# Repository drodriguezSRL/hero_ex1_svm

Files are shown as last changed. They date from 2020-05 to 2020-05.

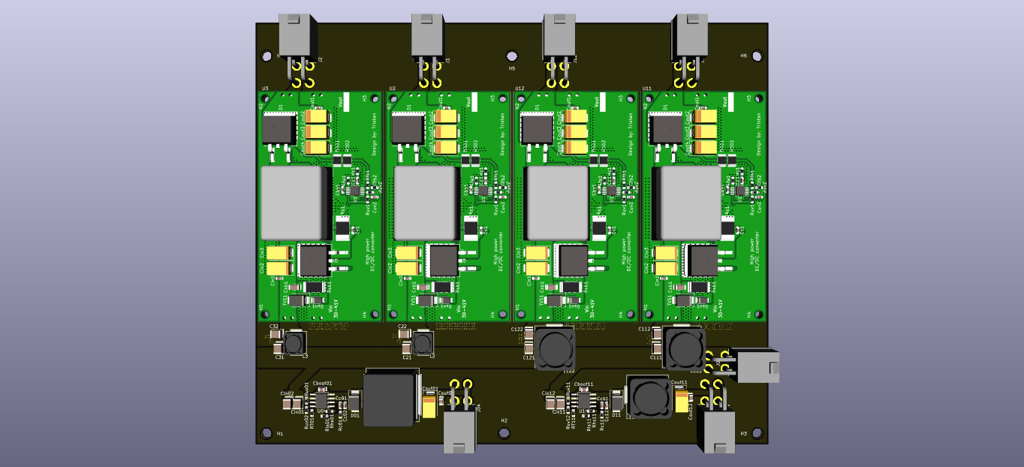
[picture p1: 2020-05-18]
Service Module/Power Conditioning & Distribution Electronics/Power Supply Unit/High_power__DC_DC_board/Doc/Power_board_preview_top.png

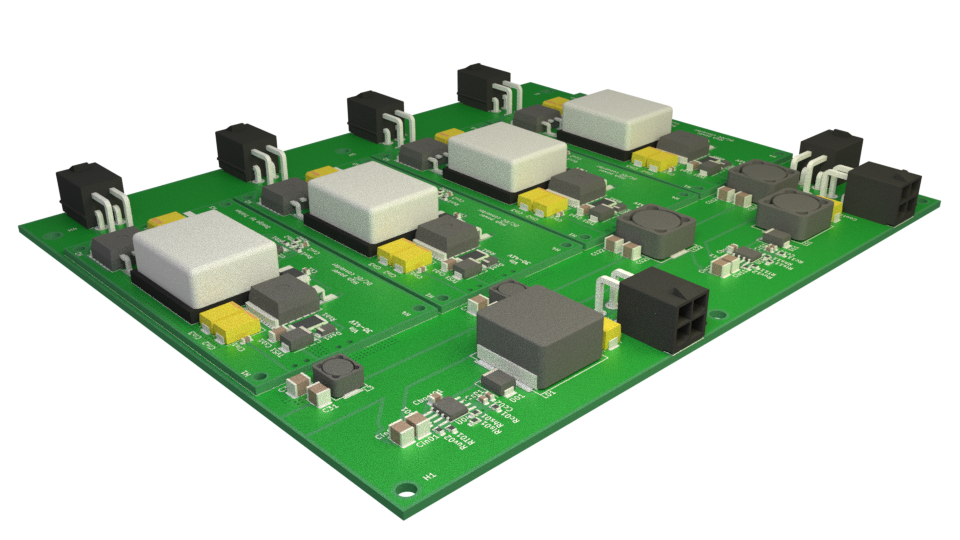
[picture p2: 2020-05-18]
Service Module/Power Conditioning & Distribution Electronics/Power Supply Unit/High_power__DC_DC_board/Doc/low_res_power_board.png

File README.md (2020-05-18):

# HERO Explorer 1 Rover - Service Module (SVM)

The following contains all the design files (i.e., kiCad project files) for the PCBs inside the service module. That includes the Power Supply Unit (PSU), Power Distribution Unit (PDU), and the Rocker Interface Unit (RIU).  3D graphics files are also included (.step and .stl).

## Versioning

High-speed Exploration Rover Team, Explorer 1 Service Module SVM Version 1. Rev. 0.

## Authors

* **David Rodriguez** - *Head of the project*
* **Alan Allart** - *Electronics & Low-level developer*

See also a list of contributors

* **Kazuki Nakagoshi** - *Manufacturing & International relationships*
* **Tristan Lecocq** - *Power system*
* **Sayo Sugimori** - *Secretary*
* **Kazuya Yoshida** - *Professor, Space Robotics Lab*

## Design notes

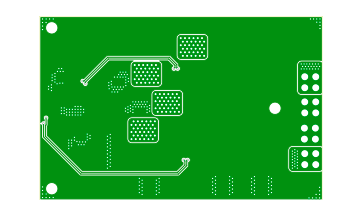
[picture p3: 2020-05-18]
Service Module/Power Conditioning & Distribution Electronics/Power Supply Unit/High_power_DC_DC_buck_boost_converter/Buck_boost/Doc/Buck_boost-brd.png

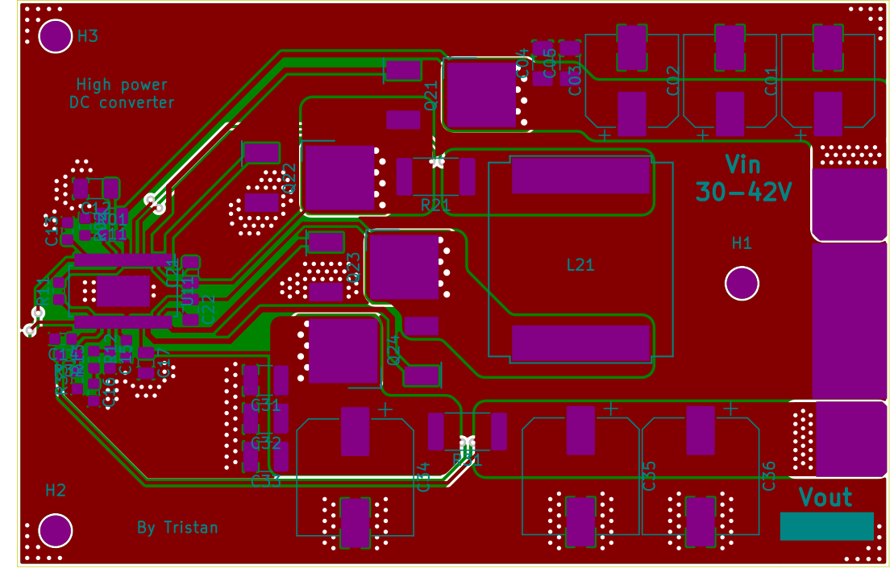
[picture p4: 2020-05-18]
Service Module/Power Conditioning & Distribution Electronics/Power Supply Unit/High_power_DC_DC_buck_boost_converter/Buck_boost/Doc/PCB.png

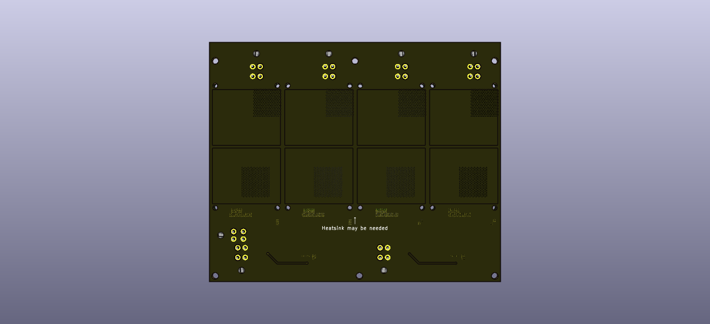
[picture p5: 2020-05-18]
Service Module/Power Conditioning & Distribution Electronics/Power Supply Unit/High_power__DC_DC_board/Doc/Power_board_preview_bot.png

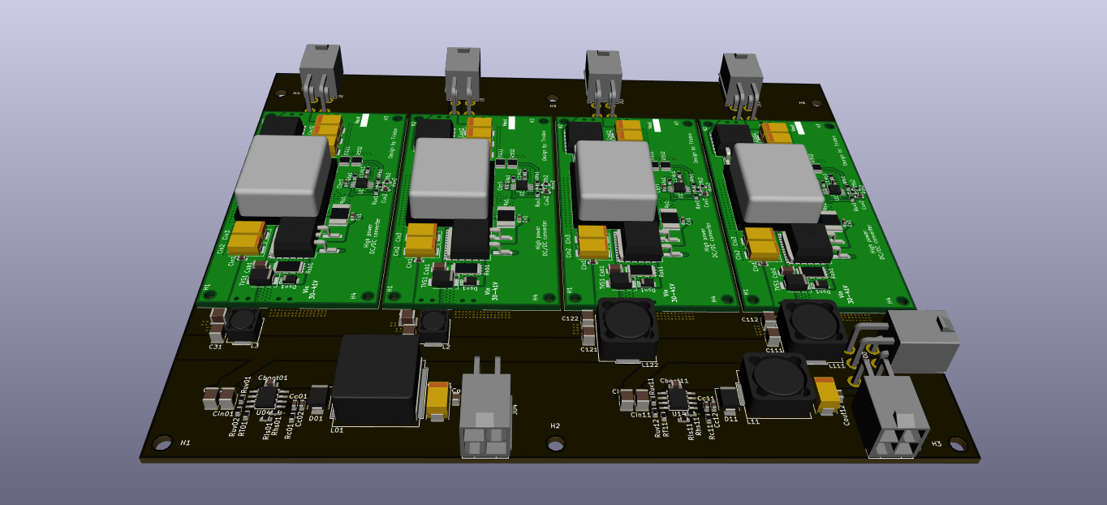
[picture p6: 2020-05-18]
Service Module/Power Conditioning & Distribution Electronics/Power Supply Unit/High_power__DC_DC_board/Doc/Power_board_preview.png

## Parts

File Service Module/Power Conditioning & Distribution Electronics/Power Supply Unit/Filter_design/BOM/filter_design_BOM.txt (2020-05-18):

###########################################
#   Bill of materials for Filter Design   #
###########################################

Prices are took from Mouser.jp website

#############################################

    Description         Reference           nb      price(¥)    unit_price(¥)

    10u L IDC>7.5A      744373965100        2       654,8       327.4
    10u L IDC>3.5A      PA4341.103ANLT      2       244.6       122.3
    1210 470n / 50V C   C1210C474K5RACTU    8       252         31.5 

#############################################

Total components price (per board): 1151,4¥

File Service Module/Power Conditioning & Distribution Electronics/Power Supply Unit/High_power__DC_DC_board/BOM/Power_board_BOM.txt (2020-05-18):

#############################################
#   Bill of materials for Power Board PCB   #
#############################################

Prices are took from Mouser.jp website

#############################################

Name            Description     Reference           nb      price(¥)    unit_price(¥)

Buck converter:
U05,U15         ADJ converter   TPS54560BDDA        x2      1367,8      683.9

Passive components:
Cboot           0.1u/50V C      885012206095        x2      23.4        11.7
Cc01            27n/25V C       CC0603KRX7R8BB273   x1      14          14
Cc02            680p/25V C      885012206058        x1      11.7        11.7
Cc11            18n/25V C       CC0603KRX7R8BB183   x1      14          14
Cc12            1n/25V C        CC0603KRX7R8BB102   x1      11.7        11.7
Cin             10u/50V C       GRM32ER71H106MA12L  x4      447,2       111.8
Cout01,Cout11   47u/50V CP      T495X476K035ATE230  x2      549,8       274.9
Cout02,Cout12   100n/50V C      885012207098        x2      23.4        11.7
D01,D02         Shottky D       NRVTSS5100ET3G      x2      109,6       54.8
L01             47u/3A L        177CDMCCDS-470MC    x1      454.4       454.4
L11             22u/3A L        125CDMCCDS-220MC    x1      210.9       210.9
Rc01            0603 6.8k R     CRCW06036K80FKEA    x1      11.7        11.7
Rc11            0603 4.42k R    CRCW06034K42FKEA    x1      11.7        11.7
Rhs01           0603 46.4k R    CRCW060346K4FKEA    x1      11.7        11.7
Rhs11           0603 17.4k R    CRCW060317K4FKEA    x1      11.7        11.7
Rls01,Rls11     0603 3.3k R     CRCW06033K30FKEA    x2      23.4        11.7
RT01,RT11       0603 243k R     CRCW0603243KFKEA    x2      23.4        11.7
Ruv01,Ruv11     0603 294k R     CRCW0603294KFKEA    x2      23.4        11.7
Ruv02,Ruv12     0603 12.1k R    CRCW060312K1FKEA    x2      23.4        11.7

Connectors :
JXX             Molex conn      172448-0004         x7      611,8       87.4

#############################################

Total components price (per board): 3990,1¥

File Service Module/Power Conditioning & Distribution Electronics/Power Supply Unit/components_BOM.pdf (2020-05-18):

## Components listing for 4 High power DC/DC converter modules + 1 Power Board

### Price taken from Mouser.jp website without quantity price reduction

Component ref. | Description | Purchase link | Number

DC/DC module components
LT8390EFE#PBF | Buck + boost DC controller | 1277,8 | 5 | 6389
NTD5C668NLT4G | Power N-MOSFET | 188,4 | 20 | 3768
EEETG1H470P | 47uF / 50V electrolytic filtering capacitor | 108,9 | 15 | 1633,5
EEETG1H100P | 10uF / 50V electrolytic filtering capacitor | 88,5 | 15 | 1327,5
GCM32EL8EH106KA07L | 10uF / 50V ceramic filtering capacitor | 144,1 | 15 | 2161,5
C1206C475M5RACAUTO | 4,7uF / 50V ceramic filtering capacitor | 77,2 | 10 | 772
C0805X104K1RAC3316 | 0,1uF / 100V bootstrap capacitor | 49,9 | 10 | 499
CC0805KFX7R9BB105 | 1uF / 50V decoupling capacitor | 29,5 | 10 | 295
CC1206KKX5R9BB475 | 4,7uF / 50V decoupling capacitor | 81,7 | 6 | 490,2
CC0603KRX5R9BB474 | 0,47uF / 50V decoupling capacitor | 67 | 6 | 402
CC0603JPX7R9BB104 | 0,1uF / 50V soft start capacitor | 14,8 | 6 | 88,8
CC0603GPNPO9BN101 | 100pF / 50V compensation capacitor | 14,8 | 6 | 88,8
CC0603KRX7R9BB472 | 4,7nF / 50V compensation capacitor | 11,3 | 6 | 67,8
CRCW0603120KFKEA | 120k UVLO resistor | 11,3 | 6 | 67,8
CRCW06035K10FKEA | 5,1k UVLO resistor | 11,3 | 6 | 67,8
CRCW0603100KFKEA | | 11,3 | 20 | 226
CRCW060327K0JNEA | 27k compensation resistor | 11,3 | 6 | 67,8
PA4344.333ANLT | 33uH / 12A High power inductor | 514,1 | 6 | 3084,6
CRCW0603150KFKEA | 150k FB resistor (36V reg) | 11,3 | 4 | 45,2
TNPW06034K27BEEA | 4,27k FB resistor (36V reg) | 76 | 4 | 304
PMR100HZPJU9L0 | 9mOhm / 2W shunt resistor | 56,7 | 3 | 170,1
RLP73V3AR011FTDF | 11mOhm / 2W shunt resistor | 85,1 | 6 | 510,6
RT0603DRE077K41L | 7,41k FB resistor (14,5V reg) | 14,8 | 2 | 29,6
RLP73V3AR013FTDF | 13mOhm / 2W shunt resistor | 85,1 | 3 | 255,3
CRCW06034K30FKEA | 4,3k FB resistor (24V reg) | 11,3 | 2 | 22,6
| | | | 22834,5
Filtering components
744373965100 | IDC=8,8A 10uH filtering inductor | 327,4 | 3 | 982,2
PA4341.103ANLT | IDC=4A 10uH filtering inductor | 122,3 | 3 | 366,9
C1210C474K5RACTU | 470nF / 50V filtering capacitor | 31,5 | 10 | 315
| | PRICE | 16 | 1664,1
Power Board components
TPS54560BDDA | 5A adustable buck converter | 683,9 | 4 | 2735,6
885012206095 | 0,1uF / 50V bootstap capacitor | 11,7 | 4 | 46,8
CC0603KRX7R8BB273 | 27nF / 25V Compensation capacitor | 14 | 2 | 28
885012206058 | 680pF / 25V Compensation capacitor | 11,7 | 2 | 23,4
CC0603KRX7R8BB183 | 18nF / 25V Compensation capacitor | 14 | 2 | 28
CC0603KRX7R8BB102 | 1nF / 25V Compensation capacitor | 11,7 | 2 | 23,4
GRM32ER71H106MA12L | 10uF / 50V Input capacitor | 111,8 | 8 | 894,4
T495X476K035ATE230 | 47uF / 50V Output tantalum capacitor | 274,9 | 4 | 1099,6
885012207098 | 100nF / 50V Output ceramic capacitor | 11,7 | 4 | 46,8
NRVTSS5100ET3G | Schottky rectifier diode | 54,8 | 4 | 219,2
177CDMCCDS-470MC | 47uH fixed inductor | 454,4 | 2 | 908,8
125CDMCCDS-220MC | 22uH fixed inductor | 210,9 | 2 | 421,8
CRCW06036K80FKEA | 0603 6,8kOhm compensation resistor | 11,7 | 2 | 23,4
CRCW06034K42FKEA | 0603 4,42kOhm compensation resistor | 11,7 | 2 | 23,4
CRCW060346K4FKEA | 0603 46,4kOhm feedback resistor | 11,7 | 2 | 23,4
CRCW060317K4FKEA | 0603 17,4kOhm feedback resistor | 11,7 | 2 | 23,4
CRCW06033K30FKEA | 0603 3,3kOhm feedback resistor | 11,7 | 4 | 46,8
CRCW0603243KFKEA | 0603 243kOhm frequency set resistor | 11,7 | 4 | 46,8
CRCW0603294KFKEA | 0603 294kOhm undervoltage resistor | 11,7 | 4 | 46,8
CRCW060312K1FKEA | 0603 12,1k undervoltage resistor | 11,7 | 4 | 46,8
172448-0004 | 13A/contact horizontal Molex connectors | 87,4 | 10 | 874
| | PRICE | 74 | 7630,6
Other
TS391AX10 | Solder paste | 3139,7 | 1 | 3139,7
100500F00000G | Thermal paste | 3458,9 | 1 | 3458,9
| | PRICE | 2 | 6598,6
TOTAL PRICE | 92 | 38727,8
Unit price ( ¥ ) | Price ( ¥ )

https://www.mouser.jp/ProductDetail/Analog-Devices-Linear-Technology/LT8390EFEPBF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
100k FB / frequency set / bias resistor | https://www.mouser.jp/ProductDetail/Vishay-Dale/CRCW0603100KFKEA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
https://www.mouser.jp/ProductDetail/Vishay-Dale/CRCW060327K0JNEA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

https://www.mouser.jp/ProductDetail/Wurth-Elektronik/744373965100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

https://www.mouser.jp/ProductDetail/Texas-Instruments/TPS54560BDDA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

https://www.mouser.jp/ProductDetail/Chip-Quik/TS391AX10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

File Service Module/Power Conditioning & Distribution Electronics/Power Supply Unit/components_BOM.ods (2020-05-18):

Components listing for 4 High power DC/DC converter modules + 1 Power Board
Price taken from Mouser.jp website without quantity price reduction
Component ref. | Description | Purchase link | Unit price ( ¥ ) | Number | Price ( ¥ )
DC/DC module components
LT8390EFE#PBF | Buck + boost DC controller | https://www.mouser.jp/ProductDetail/Analog-Devices-Linear-Technology/LT8390EFEPBF | 1277,8 | 5 | 6389
NTD5C668NLT4G | Power N-MOSFET | https://www.mouser.jp/ProductDetail/ON-Semiconductor/NTD5C668NLT4G | 188,4 | 20 | 3768
EEETG1H470P | 47uF / 50V electrolytic filtering capacitor | https://www.mouser.jp/ProductDetail/Panasonic/EEE-TG1H470P | 108,9 | 15 | 1633,5
EEETG1H100P | 10uF / 50V electrolytic filtering capacitor | https://www.mouser.jp/ProductDetail/Panasonic/EEE-TG1H100P | 88,5 | 15 | 1327,5
GCM32EL8EH106KA07L | 10uF / 50V ceramic filtering capacitor | https://www.mouser.jp/ProductDetail/Murata-Electronics/GCM32EL8EH106KA07L | 144,1 | 15 | 2161,5
C1206C475M5RACAUTO | 4,7uF / 50V ceramic filtering capacitor | https://www.mouser.jp/ProductDetail/KEMET/C1206C475M5RACAUTO | 77,2 | 10 | 772
C0805X104K1RAC3316 | 0,1uF / 100V bootstrap capacitor | https://www.mouser.jp/ProductDetail/KEMET/C0805X104K1RAC3316 | 49,9 | 10 | 499
CC0805KFX7R9BB105 | 1uF / 50V decoupling capacitor | https://www.mouser.jp/ProductDetail/Yageo/CC0805KFX7R9BB105 | 29,5 | 10 | 295
CC1206KKX5R9BB475 | 4,7uF / 50V decoupling capacitor | https://www.mouser.jp/ProductDetail/Yageo/CC1206KKX5R9BB475 | 81,7 | 6 | 490,2
CC0603KRX5R9BB474 | 0,47uF / 50V decoupling capacitor | https://www.mouser.jp/ProductDetail/Yageo/CC0603KRX5R9BB474 | 67 | 6 | 402
CC0603JPX7R9BB104 | 0,1uF / 50V soft start capacitor | https://www.mouser.jp/ProductDetail/Yageo/CC0603JPX7R9BB104 | 14,8 | 6 | 88,8
CC0603GPNPO9BN101 | 100pF / 50V compensation capacitor | https://www.mouser.jp/ProductDetail/Yageo/CC0603GPNPO9BN101 | 14,8 | 6 | 88,8
CC0603KRX7R9BB472 | 4,7nF / 50V compensation capacitor | https://www.mouser.jp/ProductDetail/Yageo/CC0603KRX7R9BB472 | 11,3 | 6 | 67,8
CRCW0603120KFKEA | 120k UVLO resistor | https://www.mouser.jp/ProductDetail/Vishay-Dale/CRCW0603120KFKEA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 | 11,3 | 6 | 67,8
CRCW06035K10FKEA | 5,1k UVLO resistor | https://www.mouser.jp/ProductDetail/Vishay-Dale/CRCW06035K10FKEA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 | 11,3 | 6 | 67,8
CRCW0603100KFKEA | 100k FB / frequency set / bias resistor | https://www.mouser.jp/ProductDetail/Vishay-Dale/CRCW0603100KFKEA | 11,3 | 20 | 226
CRCW060327K0JNEA | 27k compensation resistor | https://www.mouser.jp/ProductDetail/Vishay-Dale/CRCW060327K0JNEA | 11,3 | 6 | 67,8
PA4344.333ANLT | 33uH / 12A High power inductor | https://www.mouser.jp/ProductDetail/Pulse-Electronics/PA4344333ANLT | 514,1 | 6 | 3084,6
CRCW0603150KFKEA | 150k FB resistor (36V reg) | https://www.mouser.jp/ProductDetail/Vishay-Dale/CRCW0603150KFKEA | 11,3 | 4 | 45,2
TNPW06034K27BEEA | 4,27k FB resistor (36V reg) | https://www.mouser.jp/ProductDetail/Vishay/TNPW06034K27BEEA | 76 | 4 | 304
PMR100HZPJU9L0 | 9mOhm / 2W shunt resistor | https://www.mouser.jp/ProductDetail/ROHM-Semiconductor/PMR100HZPJU9L0 | 56,7 | 3 | 170,1
RLP73V3AR011FTDF | 11mOhm / 2W shunt resistor | https://www.mouser.jp/ProductDetail/TE-Connectivity-Holsworthy/RLP73V3AR011FTDF | 85,1 | 6 | 510,6
RT0603DRE077K41L | 7,41k FB resistor (14,5V reg) | https://www.mouser.jp/ProductDetail/Yageo/RT0603DRE077K41L | 14,8 | 2 | 29,6
RLP73V3AR013FTDF | 13mOhm / 2W shunt resistor | https://www.mouser.jp/ProductDetail/TE-Connectivity-Holsworthy/RLP73V3AR013FTDF | 85,1 | 3 | 255,3
CRCW06034K30FKEA | 4,3k FB resistor (24V reg) | https://www.mouser.jp/ProductDetail/Vishay-Dale/CRCW06034K30FKEA | 11,3 | 2 | 22,6
 |  |  |  |  | 22834,5
Filtering components
744373965100 | IDC=8,8A 10uH filtering inductor | https://www.mouser.jp/ProductDetail/Wurth-Elektronik/744373965100 | 327,4 | 3 | 982,2
PA4341.103ANLT | IDC=4A 10uH filtering inductor | https://www.mouser.jp/ProductDetail/Pulse-Electronics/PA4341103ANLT | 122,3 | 3 | 366,9
C1210C474K5RACTU | 470nF / 50V filtering capacitor | https://www.mouser.jp/ProductDetail/KEMET/C1210C474K5RACTU?qs=sGAEpiMZZMs0AnBnWHyRQM0yVqKBBK3frSa2n3pwvnQ%3D | 31,5 | 10 | 315
 |  |  | PRICE | 16 | 1664,1
Power Board components
TPS54560BDDA | 5A adustable buck converter | https://www.mouser.jp/ProductDetail/Texas-Instruments/TPS54560BDDA | 683,9 | 4 | 2735,6
885012206095 | 0,1uF / 50V bootstap capacitor | https://www.mouser.jp/ProductDetail/Wurth-Elektronik/885012206095 | 11,7 | 4 | 46,8
CC0603KRX7R8BB273 | 27nF / 25V Compensation capacitor | https://www.mouser.jp/ProductDetail/Yageo/CC0603KRX7R8BB273 | 14 | 2 | 28
885012206058 | 680pF / 25V Compensation capacitor | https://www.mouser.jp/ProductDetail/Wurth-Elektronik/885012206058 | 11,7 | 2 | 23,4
CC0603KRX7R8BB183 | 18nF / 25V Compensation capacitor | https://www.mouser.jp/ProductDetail/Yageo/CC0603KRX7R8BB183 | 14 | 2 | 28
CC0603KRX7R8BB102 | 1nF / 25V Compensation capacitor | https://www.mouser.jp/ProductDetail/Yageo/CC0603KRX7R8BB102 | 11,7 | 2 | 23,4
GRM32ER71H106MA12L | 10uF / 50V Input capacitor | https://www.mouser.jp/ProductDetail/Murata-Electronics/GRM32ER71H106MA12L | 111,8 | 8 | 894,4
T495X476K035ATE230 | 47uF / 50V Output tantalum capacitor | https://www.mouser.jp/ProductDetail/KEMET/T495X476K035ATE230 | 274,9 | 4 | 1099,6
885012207098 | 100nF / 50V Output ceramic capacitor | https://www.mouser.jp/ProductDetail/Wurth-Elektronik/885012207098 | 11,7 | 4 | 46,8
NRVTSS5100ET3G | Schottky rectifier diode | https://www.mouser.jp/ProductDetail/ON-Semiconductor/NRVTSS5100ET3G | 54,8 | 4 | 219,2
177CDMCCDS-470MC | 47uH fixed inductor | https://www.mouser.jp/ProductDetail/Sumida/177CDMCCDS-470MC | 454,4 | 2 | 908,8
125CDMCCDS-220MC | 22uH fixed inductor | https://www.mouser.jp/ProductDetail/Sumida/125CDMCCDS-220MC | 210,9 | 2 | 421,8
CRCW06036K80FKEA | 0603 6,8kOhm compensation resistor | https://www.mouser.jp/ProductDetail/Vishay-Dale/CRCW06036K80FKEA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 | 11,7 | 2 | 23,4
CRCW06034K42FKEA | 0603 4,42kOhm compensation resistor | https://www.mouser.jp/ProductDetail/Vishay-Dale/CRCW06034K42FKEA | 11,7 | 2 | 23,4
CRCW060346K4FKEA | 0603 46,4kOhm feedback resistor | https://www.mouser.jp/ProductDetail/Vishay-Dale/CRCW060346K4FKEA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 | 11,7 | 2 | 23,4
CRCW060317K4FKEA | 0603 17,4kOhm feedback resistor | https://www.mouser.jp/ProductDetail/Vishay-Dale/CRCW060317K4FKEA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 | 11,7 | 2 | 23,4
CRCW06033K30FKEA | 0603 3,3kOhm feedback resistor | https://www.mouser.jp/ProductDetail/Vishay-Dale/CRCW06033K30FKEA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 | 11,7 | 4 | 46,8
CRCW0603243KFKEA | 0603 243kOhm frequency set resistor | https://www.mouser.jp/ProductDetail/Vishay-Dale/CRCW0603243KFKEA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 | 11,7 | 4 | 46,8
CRCW0603294KFKEA | 0603 294kOhm undervoltage resistor | https://www.mouser.jp/ProductDetail/Vishay-Dale/CRCW0603294KFKEA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 | 11,7 | 4 | 46,8
CRCW060312K1FKEA | 0603 12,1k undervoltage resistor | https://www.mouser.jp/ProductDetail/Vishay-Dale/CRCW060312K1FKEA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 | 11,7 | 4 | 46,8
172448-0004 | 13A/contact horizontal Molex connectors | https://www.mouser.jp/ProductDetail/Molex/172448-0004 | 87,4 | 10 | 874
 |  |  | PRICE | 74 | 7630,6
Other
TS391AX10 | Solder paste | https://www.mouser.jp/ProductDetail/Chip-Quik/TS391AX10 | 3139,7 | 1 | 3139,7
100500F00000G | Thermal paste | https://www.mouser.jp/ProductDetail/Aavid/100500F00000G | 3458,9 | 1 | 3458,9
 |  |  | PRICE | 2 | 6598,6
 |  |  | TOTAL PRICE | 92 | 38727,8

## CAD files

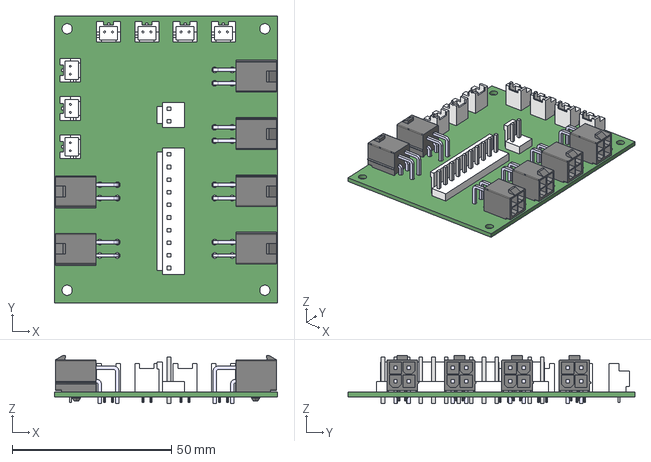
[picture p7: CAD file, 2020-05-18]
Service Module/Power Conditioning & Distribution Electronics/Power Distribution Unit/PowerDistributionUnit.step
70.0 x 90.0 x 15.1 mm

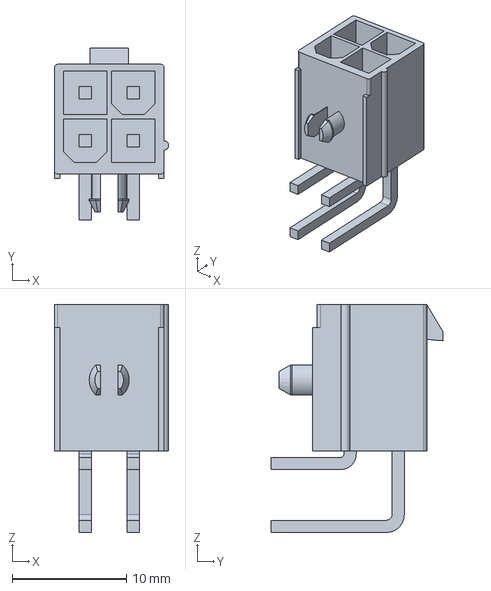
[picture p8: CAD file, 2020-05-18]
Service Module/Power Conditioning & Distribution Electronics/Power Supply Unit/High_power__DC_DC_board/power_board/3d_model/Molex_horizontal_1724480004.stp
10.0 x 15.0 x 19.9 mm

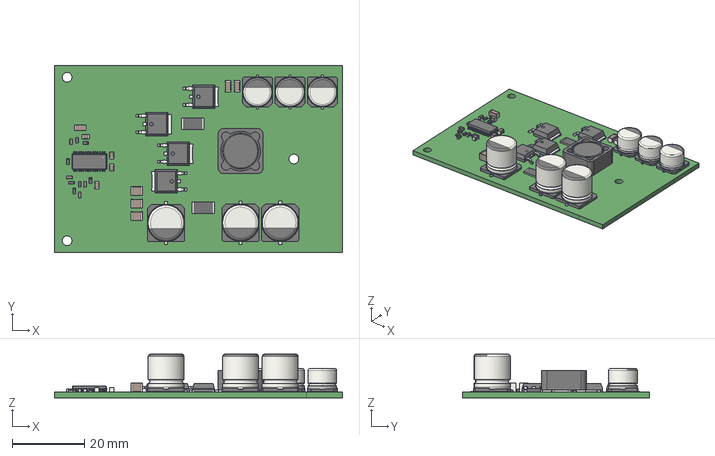
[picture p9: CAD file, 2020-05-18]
Service Module/Power Conditioning & Distribution Electronics/Power Supply Unit/High_power_DC_DC_buck_boost_converter/Buck_boost/3d_model/Buck_boost.step
80.0 x 52.0 x 12.2 mm

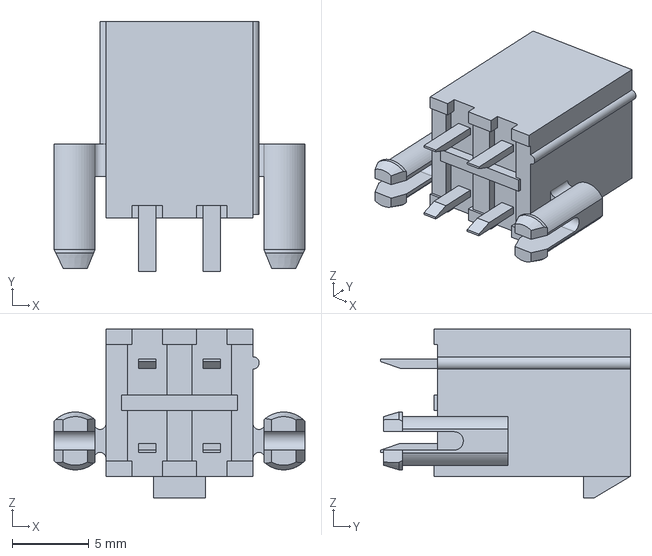
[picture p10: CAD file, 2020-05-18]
Service Module/Power Conditioning & Distribution Electronics/Power Supply Unit/High_power__DC_DC_board/power_board/3d_model/Molex_vertical_1726750413.stp
16.4 x 16.3 x 11.0 mm

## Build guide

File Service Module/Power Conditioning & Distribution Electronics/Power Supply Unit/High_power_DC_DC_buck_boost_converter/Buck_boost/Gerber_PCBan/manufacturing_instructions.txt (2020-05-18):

Buck-boost-F_Cu.gtl（部品面パターン）

Buck-boost-B_Cu.gbl（半田面パターン）

Buck-boost-F_Mask.gts（部品面パターン）

Buck-boost-B_Mask.gbs（半田面パターン）

Buck-boost-F_SilkS.gto（部品面パターン）

Buck-boost-B_SilkS.gbo（半田面パターン）

Buck-boost-Edge_Cuts.gm1　（基板外形）

Buck-boost.drl （ドリルデータ）

Buck-boost-drl_map.gbr（ドリルマップ）

Buck-boost-drl.rpt (ドリルリスト）

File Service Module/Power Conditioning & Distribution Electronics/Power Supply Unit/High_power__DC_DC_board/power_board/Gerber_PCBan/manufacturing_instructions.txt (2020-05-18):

High_power__DC_DC_board-F_Cu.gtl（部品面パターン）

High_power__DC_DC_board-B_Cu.gbl（半田面パターン）

High_power__DC_DC_board-F_Mask.gts（部品面パターン）

High_power__DC_DC_board-B_Mask.gbs（半田面パターン）

High_power__DC_DC_board-F_SilkS.gto（部品面パターン）

High_power__DC_DC_board-B_SilkS.gbo（半田面パターン）

High_power__DC_DC_board-Edge_Cuts.gm1　（基板外形）

High_power__DC_DC_board.drl （ドリルデータ）

High_power__DC_DC_board-drl_map.gbr（ドリルマップ）

High_power__DC_DC_board-drl.rpt (ドリルリスト）

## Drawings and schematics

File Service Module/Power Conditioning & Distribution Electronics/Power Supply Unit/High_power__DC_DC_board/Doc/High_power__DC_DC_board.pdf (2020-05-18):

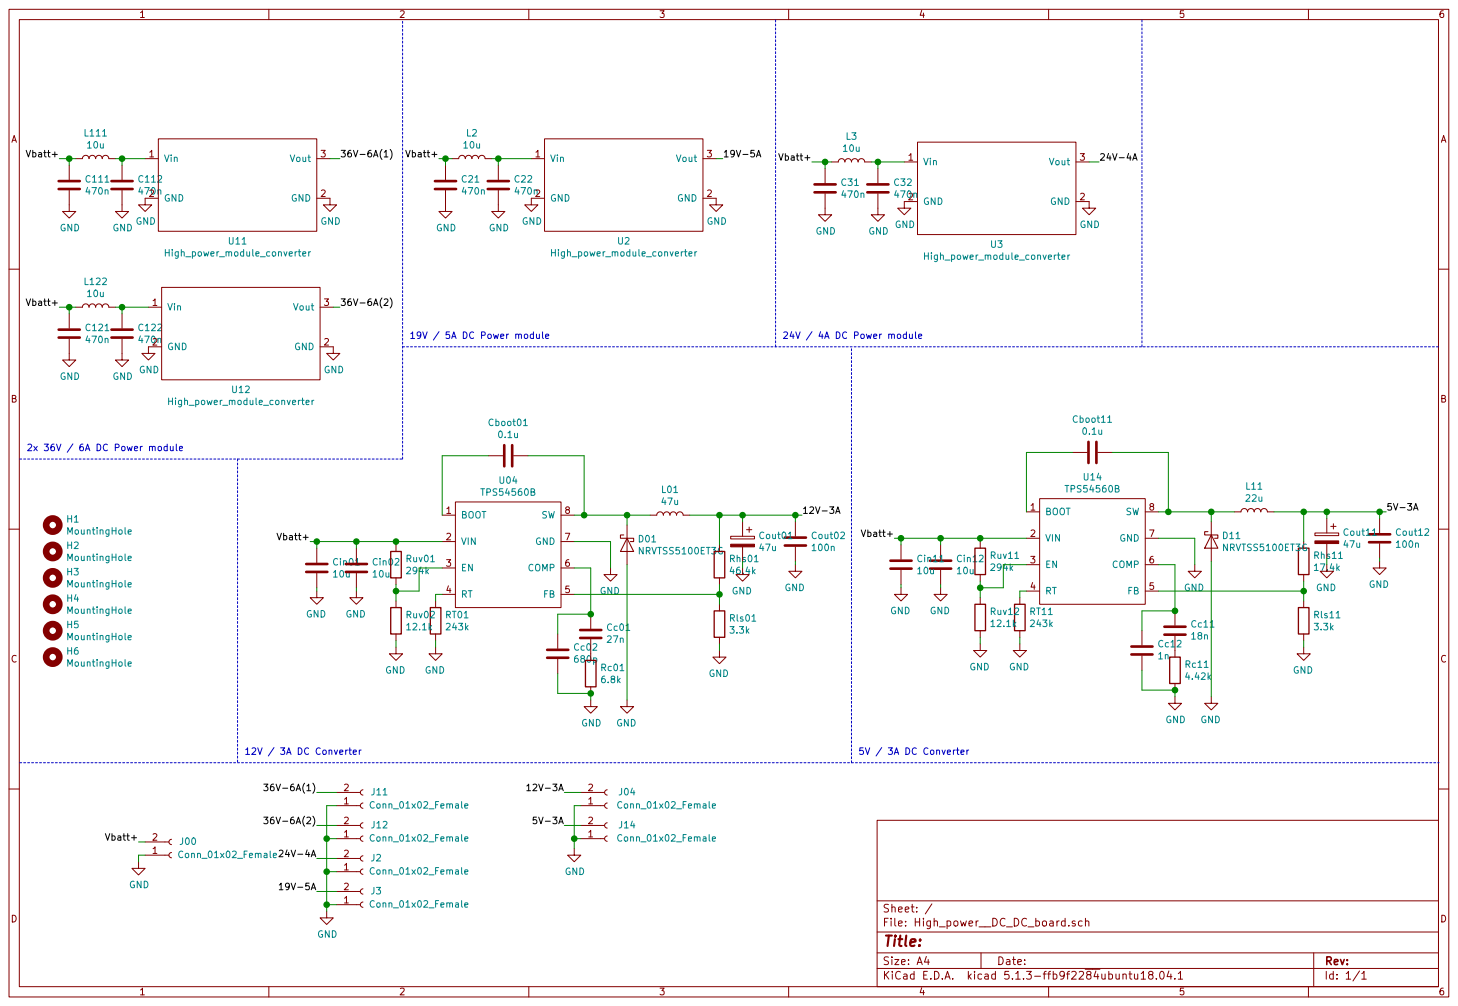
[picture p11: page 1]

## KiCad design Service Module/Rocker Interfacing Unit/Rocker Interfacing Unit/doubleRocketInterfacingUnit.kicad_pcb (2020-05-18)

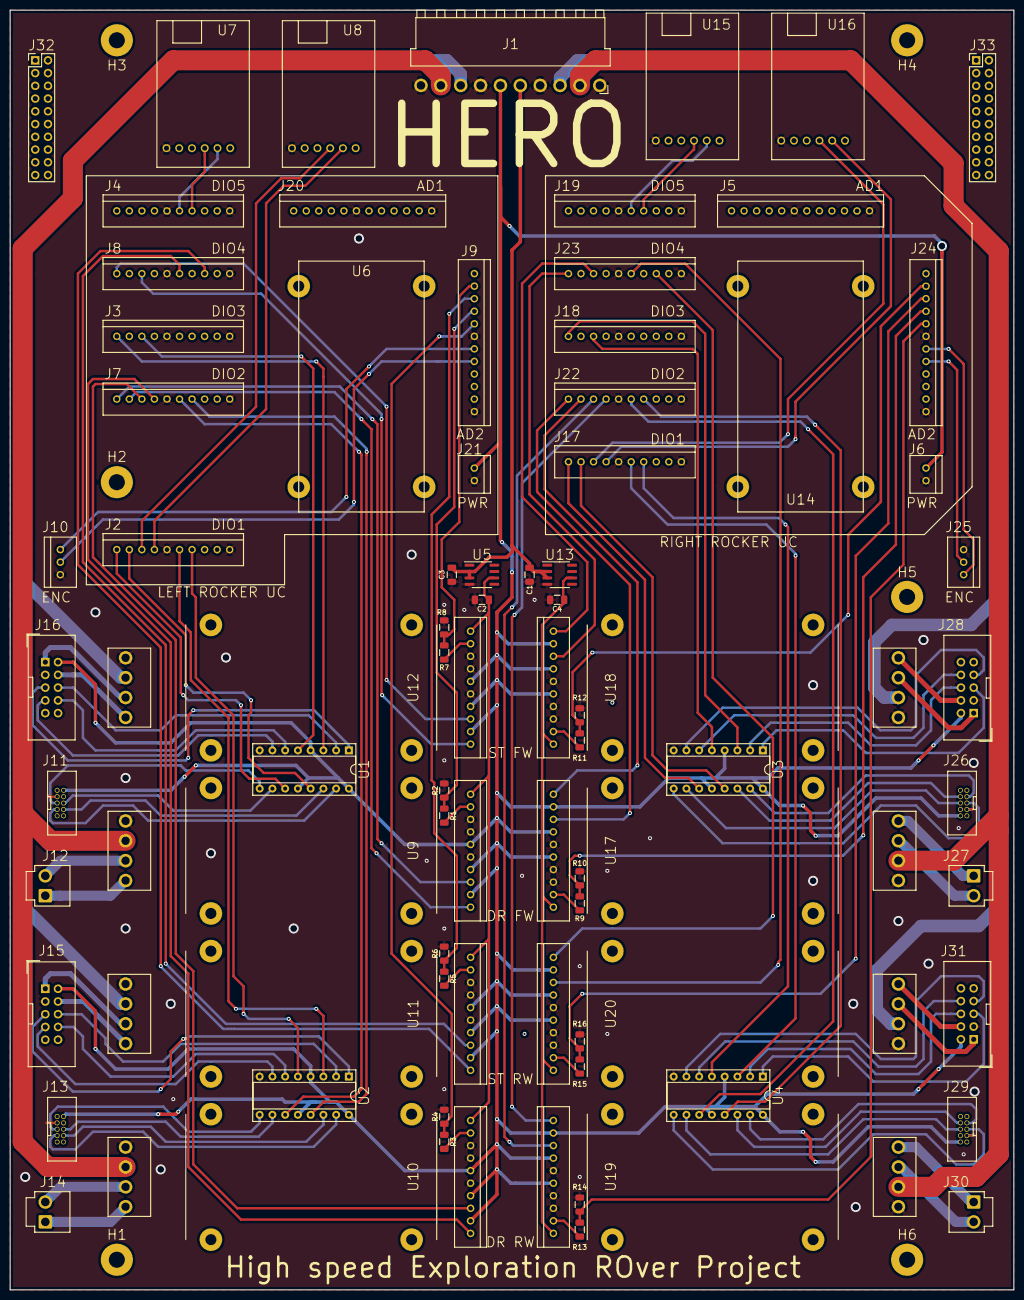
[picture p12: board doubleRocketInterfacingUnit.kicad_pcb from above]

Board: 2 copper layers, 200.0 x 255.0 mm, 79 parts (0 on the bottom side), 115 nets.

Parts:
C1, C3: 1µF; C_1206_3216Metric
C2, C4: 2µF; C_1206_3216Metric
H1, H2, H3, H4, H5, H6: MountingHole; MountingHole_3.2mm_M3_Pad
J1: Conn_01x10; JST_VH_B10PS-VH
J2, J3, J4, J7, J8, J17, J18, J19, J22, J23: Conn_01x10; JST_XA_B10B-XASK-1
J5, J9, J20, J24: Conn_01x12; JST_XA_B12B-XASK-1
J6, J21: Conn_01x02; JST_XA_B2B-XASK-1
J10, J25: Conn_01x03; JST_XA_B3B-XASK-1
J11, J13, J26, J29: Conn_02x05_Odd_Even; SAMTEC_SHF-105-01-L-D-TH
J12, J14, J27, J30: Conn_01x02; JST_VH_B2P-VH
J15, J16, J28, J31: Conn_02x05_Odd_Even; IDC-Header_2x05_P2.54mm_Vertical
J32, J33: Conn_02x10_Odd_Even; PinHeader_2x10_P2.54mm_Vertical
R1, R3, R5, R7, R9, R11, R13, R15: 4k7; R_1206_3216Metric
R2, R4, R6, R8, R10, R12, R14, R16: 9k1; R_1206_3216Metric
U1, U2, U3, U4: SN75175; DIP-16_W7.62mm_SocketAndIC
U5, U13: LT1461CCS8-5; SOIC-8_3.9x4.9mm_P1.27mm
U6, U14: HiBot-Titech-M4; HibotTitechM4
U7, U8, U15, U16: FTDI-Breakout-Board
U9, U10, U11, U12, U17, U18, U19, U20: HiBot-UM-1XH; HibotUM1XH

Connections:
+5V: J1.6, J6.1, J11.2, J13.2, J15.2, J16.2, J21.1, J26.2, J28.2, J29.2, J31.2, U1.4, U1.12, U1.16, U2.4, U2.12, U2.16, U3.4, U3.12, U3.16, U4.4, U4.12, U4.16, U9.5, U9.7, U9.9, U10.5, U10.7, U10.9, U11.5, U11.7, U11.9, U12.5, U12.7, U12.9, U17.5, U17.7, U17.9, U18.5, U18.7, U18.9, U19.5, U19.7, U19.9, U20.5, U20.7, U20.9
+12V: C1.1, C3.1, J1.5, U5.2, U5.3, U13.2, U13.3
+24V: J1.3, J1.8, U11.13, U12.13, U18.13, U20.13
+36V: J1.2, J1.9, U9.13, U10.13, U17.13, U19.13
/Left Rocker Interface/+3V3A: J9.7, J10.1
/Left Rocker Interface/+5VA: C2.1, U5.6, U9.1, U10.1, U11.1, U12.1
/Left Rocker Interface/CUR_DR_FW: J9.4, R1.1, R2.1
/Left Rocker Interface/CUR_DR_RW: J9.5, R3.1, R4.1
/Left Rocker Interface/CUR_ST_FW: J9.2, R7.1, R8.1
/Left Rocker Interface/CUR_ST_RW: J9.3, R5.1, R6.1
/Left Rocker Interface/ENC_DR_FW_1: J2.1, U1.11
/Left Rocker Interface/ENC_DR_FW_2: J2.2, U1.13
/Left Rocker Interface/ENC_DR_RW_1: J7.6, U2.11
/Left Rocker Interface/ENC_DR_RW_2: J7.7, U2.13
/Left Rocker Interface/ENC_ST_FW_1: J3.1, U1.3
/Left Rocker Interface/ENC_ST_FW_2: J3.3, U1.5
/Left Rocker Interface/ENC_ST_RW_1: J2.6, U2.3
/Left Rocker Interface/ENC_ST_RW_2: J2.7, U2.5
/Left Rocker Interface/Left Driving Motor Driver FW/A: J11.6, U1.10
/Left Rocker Interface/Left Driving Motor Driver FW/B: J11.8, U1.14
/Left Rocker Interface/Left Driving Motor Driver FW/~A~: J11.5, U1.9
/Left Rocker Interface/Left Driving Motor Driver FW/~B~: J11.7, U1.15
/Left Rocker Interface/Left Driving Motor Driver RW/A: J13.6, U2.10
/Left Rocker Interface/Left Driving Motor Driver RW/B: J13.8, U2.14
/Left Rocker Interface/Left Driving Motor Driver RW/~A~: J13.5, U2.9
/Left Rocker Interface/Left Driving Motor Driver RW/~B~: J13.7, U2.15
/Left Rocker Interface/Left Steering Motor Driver FW/A: J16.6, U1.2
/Left Rocker Interface/Left Steering Motor Driver FW/B: J16.8, U1.6
/Left Rocker Interface/Left Steering Motor Driver FW/~A~: J16.5, U1.1
/Left Rocker Interface/Left Steering Motor Driver FW/~B~: J16.7, U1.7
/Left Rocker Interface/Left Steering Motor Driver RW/A: J15.6, U2.2
/Left Rocker Interface/Left Steering Motor Driver RW/B: J15.8, U2.6
/Left Rocker Interface/Left Steering Motor Driver RW/~A~: J15.5, U2.1
/Left Rocker Interface/Left Steering Motor Driver RW/~B~: J15.7, U2.7
/Left Rocker Interface/MOT_DR_FW_1: J7.1, U9.8
/Left Rocker Interface/MOT_DR_FW_2: J7.2, U9.10
/Left Rocker Interface/MOT_DR_RW_1: J7.3, U10.8
/Left Rocker Interface/MOT_DR_RW_2: J7.4, U10.10
/Left Rocker Interface/MOT_ST_FW_1: J8.1, U12.8
/Left Rocker Interface/MOT_ST_FW_2: J8.3, U12.10
/Left Rocker Interface/MOT_ST_RW_1: J8.6, U11.8
/Left Rocker Interface/MOT_ST_RW_2: J8.8, U11.10
/Left Rocker Interface/POS_RK: J9.8, J10.2
/Left Rocker Interface/UART_RX_COM: J4.7, U7.3
/Left Rocker Interface/UART_RX_DBG: J2.3, U8.3
/Left Rocker Interface/UART_TX_COM: J4.6, U7.2
/Left Rocker Interface/UART_TX_DBG: J2.4, U8.2
/Right Rocker Interface/+3V3A: J24.7, J25.1
/Right Rocker Interface/+5VA: C4.1, U13.6, U17.1, U18.1, U19.1, U20.1
/Right Rocker Interface/CUR_DR_FW: J24.4, R9.1, R10.1
/Right Rocker Interface/CUR_DR_RW: J24.5, R13.1, R14.1
/Right Rocker Interface/CUR_ST_FW: J24.2, R11.1, R12.1
/Right Rocker Interface/CUR_ST_RW: J24.3, R15.1, R16.1
/Right Rocker Interface/ENC_DR_FW_1: J17.1, U3.11
/Right Rocker Interface/ENC_DR_FW_2: J17.2, U3.13
/Right Rocker Interface/ENC_DR_RW_1: J22.6, U4.11
/Right Rocker Interface/ENC_DR_RW_2: J22.7, U4.13
/Right Rocker Interface/ENC_ST_FW_1: J18.1, U3.3
/Right Rocker Interface/ENC_ST_FW_2: J18.3, U3.5
/Right Rocker Interface/ENC_ST_RW_1: J17.6, U4.3
/Right Rocker Interface/ENC_ST_RW_2: J17.7, U4.5
/Right Rocker Interface/MOT_DR_FW_1: J22.1, U17.8
/Right Rocker Interface/MOT_DR_FW_2: J22.2, U17.10
/Right Rocker Interface/MOT_DR_RW_1: J22.3, U19.8
/Right Rocker Interface/MOT_DR_RW_2: J22.4, U19.10
/Right Rocker Interface/MOT_ST_FW_1: J23.1, U18.8
/Right Rocker Interface/MOT_ST_FW_2: J23.3, U18.10
/Right Rocker Interface/MOT_ST_RW_1: J23.6, U20.8
/Right Rocker Interface/MOT_ST_RW_2: J23.8, U20.10
/Right Rocker Interface/POS_RK: J24.8, J25.2
/Right Rocker Interface/Right Driving Motor Driver FW/A: J26.6, U3.10
/Right Rocker Interface/Right Driving Motor Driver FW/B: J26.8, U3.14
/Right Rocker Interface/Right Driving Motor Driver FW/~A~: J26.5, U3.9
/Right Rocker Interface/Right Driving Motor Driver FW/~B~: J26.7, U3.15
/Right Rocker Interface/Right Driving Motor Driver RW/A: J29.6, U4.10
/Right Rocker Interface/Right Driving Motor Driver RW/B: J29.8, U4.14
/Right Rocker Interface/Right Driving Motor Driver RW/~A~: J29.5, U4.9
/Right Rocker Interface/Right Driving Motor Driver RW/~B~: J29.7, U4.15
/Right Rocker Interface/Right Steering Motor Driver FW/A: J28.6, U3.2
/Right Rocker Interface/Right Steering Motor Driver FW/B: J28.8, U3.6
/Right Rocker Interface/Right Steering Motor Driver FW/~A~: J28.5, U3.1
/Right Rocker Interface/Right Steering Motor Driver FW/~B~: J28.7, U3.7
/Right Rocker Interface/Right Steering Motor Driver RW/A: J31.6, U4.2
/Right Rocker Interface/Right Steering Motor Driver RW/B: J31.8, U4.6
/Right Rocker Interface/Right Steering Motor Driver RW/~A~: J31.5, U4.1
/Right Rocker Interface/Right Steering Motor Driver RW/~B~: J31.7, U4.7
/Right Rocker Interface/UART_RX_COM: J19.7, U15.3
/Right Rocker Interface/UART_RX_DBG: J17.3, U16.3
/Right Rocker Interface/UART_TX_COM: J19.6, U15.2
/Right Rocker Interface/UART_TX_DBG: J17.4, U16.2
GND: C1.2, C2.2, C3.2, C4.2, J1.1, J1.4, J1.7, J1.10, J2.5, J2.10, J3.5, J3.10, J4.5, J4.10, J5.6, J5.12, J6.2, J7.5, J7.10, J8.5, J8.10, J9.6, J9.12, J10.3, J11.3, J13.3, J15.3, J16.3, J17.5, J17.10, J18.5, J18.10, J19.5, J19.10, J20.6, J20.12, J21.2, J22.5, J22.10, J23.5, J23.10, J24.6, J24.12, J25.3, J26.3, J28.3, J29.3, J31.3, R2.2, R4.2, R6.2, R8.2, R10.2, R12.2, R14.2, R16.2, U1.8, U2.8, U3.8, U4.8, U5.4, U7.6, U8.6, U9.3, U9.4, U9.6, U9.14, U10.3, U10.4, U10.6, U10.14, U11.3, U11.4, U11.6, U11.14, U12.3, U12.4, U12.6, U12.14, U13.4, U15.6, U16.6, U17.3, U17.4, U17.6, U17.14, U18.3, U18.4, U18.6, U18.14, U19.3, U19.4, U19.6, U19.14, U20.3, U20.4, U20.6, U20.14
unnamed: J12.1, U9.11
unnamed: J12.2, U9.12
unnamed: J14.1, U10.11
unnamed: J14.2, U10.12
unnamed: J15.1, U11.12
unnamed: J15.4, U11.11
unnamed: J16.1, U12.12
unnamed: J16.4, U12.11
unnamed: J27.1, U17.11
unnamed: J27.2, U17.12
unnamed: J28.1, U18.12
unnamed: J28.4, U18.11
unnamed: J30.1, U19.11
unnamed: J30.2, U19.12
unnamed: J31.1, U20.12
unnamed: J31.4, U20.11
unnamed: R1.2, U9.2
unnamed: R3.2, U10.2
unnamed: R5.2, U11.2
unnamed: R7.2, U12.2
unnamed: R9.2, U17.2
unnamed: R11.2, U18.2
unnamed: R13.2, U19.2
unnamed: R15.2, U20.2

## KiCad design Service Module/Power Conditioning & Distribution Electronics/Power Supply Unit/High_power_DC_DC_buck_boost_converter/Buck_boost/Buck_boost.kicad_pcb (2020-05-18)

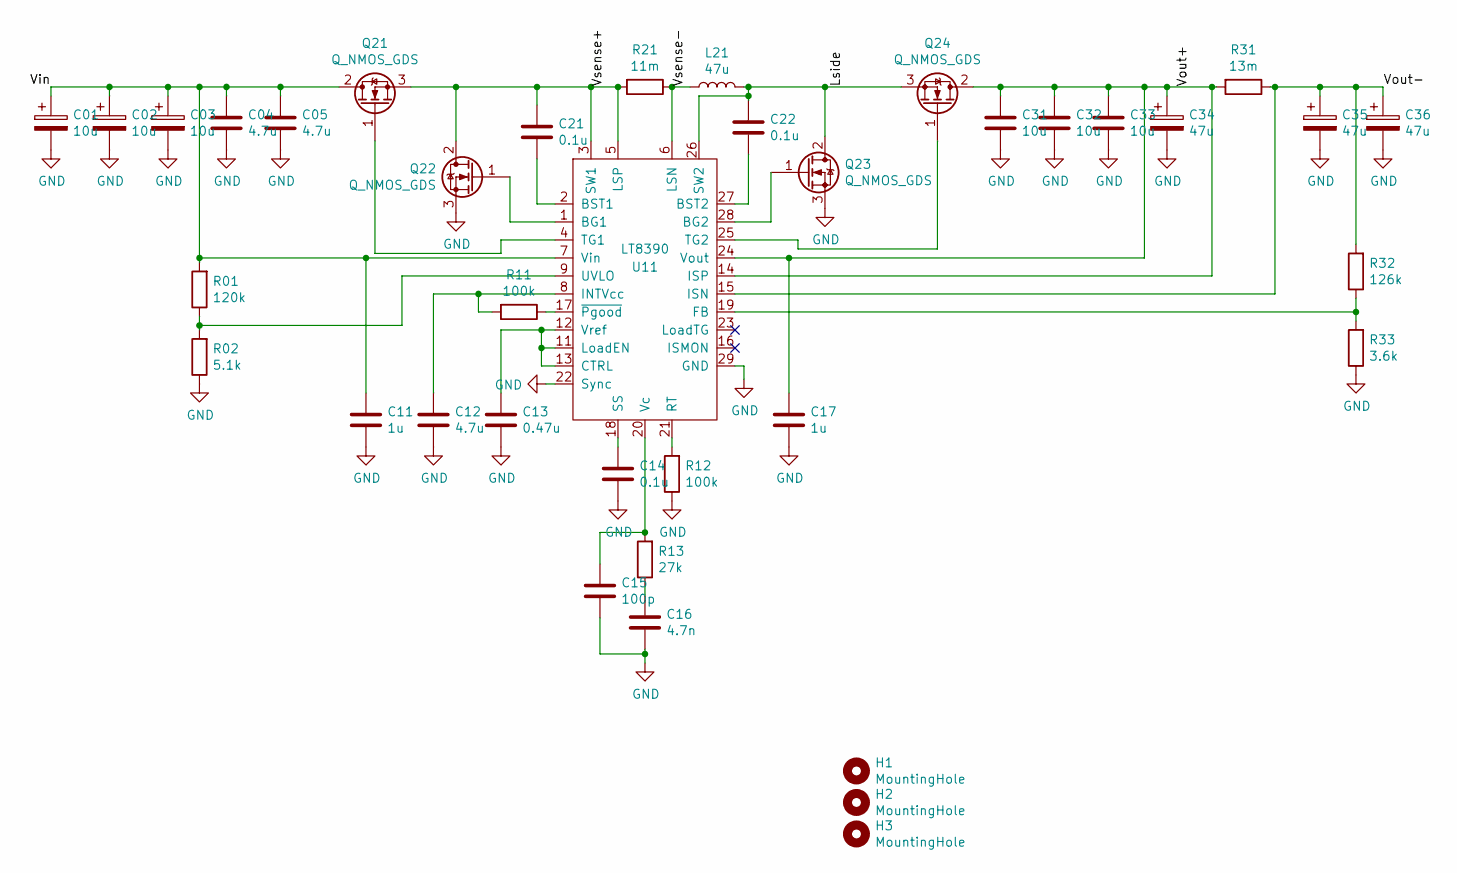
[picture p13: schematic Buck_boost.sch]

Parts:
C01, C02, C03: 10u; CP_Elec_8x6.5
C04, C05, C12: 4.7u; C_1206_3216Metric
C11, C17: 1u; C_0805_2012Metric
C13: 0.47u; C_0603_1608Metric
C14: 0.1u; C_0603_1608Metric
C15: 100p; C_0603_1608Metric
C16: 4.7n; C_0603_1608Metric
C21, C22: 0.1u; C_0805_2012Metric
C31, C32, C33: 10u; C_1210_3225Metric
C34, C35, C36: 47u; CP_Elec_10x10.5
H1, H2, H3: MountingHole; MountingHole_2.7mm_M2.5
L21: 47u; PA4344_333ANLT
Q21, Q22, Q23, Q24: Q_NMOS_GDS; DPAK
R01: 120k; R_0603_1608Metric
R02: 5.1k; R_0603_1608Metric
R11, R12: 100k; R_0603_1608Metric
R13: 27k; R_0603_1608Metric
R21: 11m; R_2512_6332Metric
R31: 13m; R_2512_6332Metric
R32: 126k; R_0603_1608Metric
R33: 3.6k; R_0603_1608Metric
U11: LT8390; TSSOP-28-1EP_4.4x9.7mm_P0.65mm

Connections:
/Lside: C22.1, L21.2, Q23.2 (D), Q24.3 (S), U11.26 (SW2)
/Vin: C01.1, C02.1, C03.1, C04.1, C05.1, C11.1, Q21.2 (D), R01.2, U11.7 (Vin)
/Vout+: C17.1, C31.1, C32.1, C33.1, C34.1, Q24.2 (D), R31.2, U11.14 (ISP), U11.24 (Vout)
/Vout-: C35.1, C36.1, R31.1, R32.2, U11.15 (ISN)
/Vsense+: C21.1, Q21.3 (S), Q22.2 (D), R21.2, U11.3 (SW1), U11.5 (LSP)
/Vsense-: L21.1, R21.1, U11.6 (LSN)
GND: C01.2, C02.2, C03.2, C04.2, C05.2, C11.2, C12.2, C13.2, C14.2, C15.2, C16.2, C17.2, C31.2, C32.2, C33.2, C34.2, C35.2, C36.2, Q22.3 (S), Q23.3 (S), R02.1, R12.1, R33.1, U11.22 (Sync), U11.29 (GND)
unnamed: C12.1, R11.2, U11.8 (INTVcc)
unnamed: C13.1, U11.11 (LoadEN), U11.12 (Vref), U11.13 (CTRL)
unnamed: C14.1, U11.18 (SS)
unnamed: C15.1, R13.2, U11.20 (Vc)
unnamed: C16.1, R13.1
unnamed: C21.2, U11.2 (BST1)
unnamed: C22.2, U11.27 (BST2)
unnamed: Q21.1 (G), U11.4 (TG1)
unnamed: Q22.1 (G), U11.1 (BG1)
unnamed: Q23.1 (G), U11.28 (BG2)
unnamed: Q24.1 (G), U11.25 (TG2)
unnamed: R01.1, R02.2, U11.9 (UVLO)
unnamed: R11.1, U11.17 (~Pgood)
unnamed: R12.2, U11.21 (RT)
unnamed: R32.1, R33.2, U11.19 (FB)

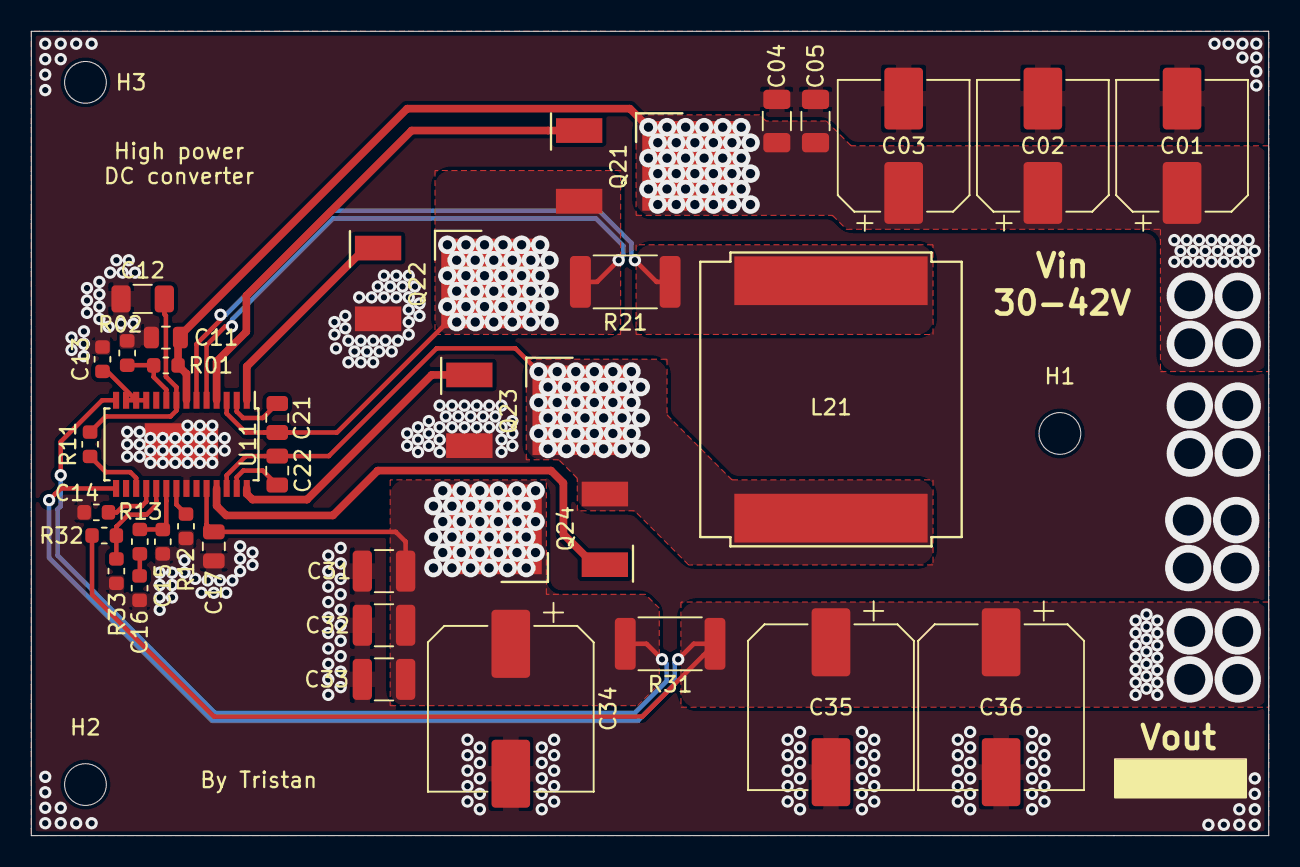
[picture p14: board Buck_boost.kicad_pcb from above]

Board: 2 copper layers, 80.0 x 52.0 mm, 38 parts (0 on the bottom side), 22 nets.

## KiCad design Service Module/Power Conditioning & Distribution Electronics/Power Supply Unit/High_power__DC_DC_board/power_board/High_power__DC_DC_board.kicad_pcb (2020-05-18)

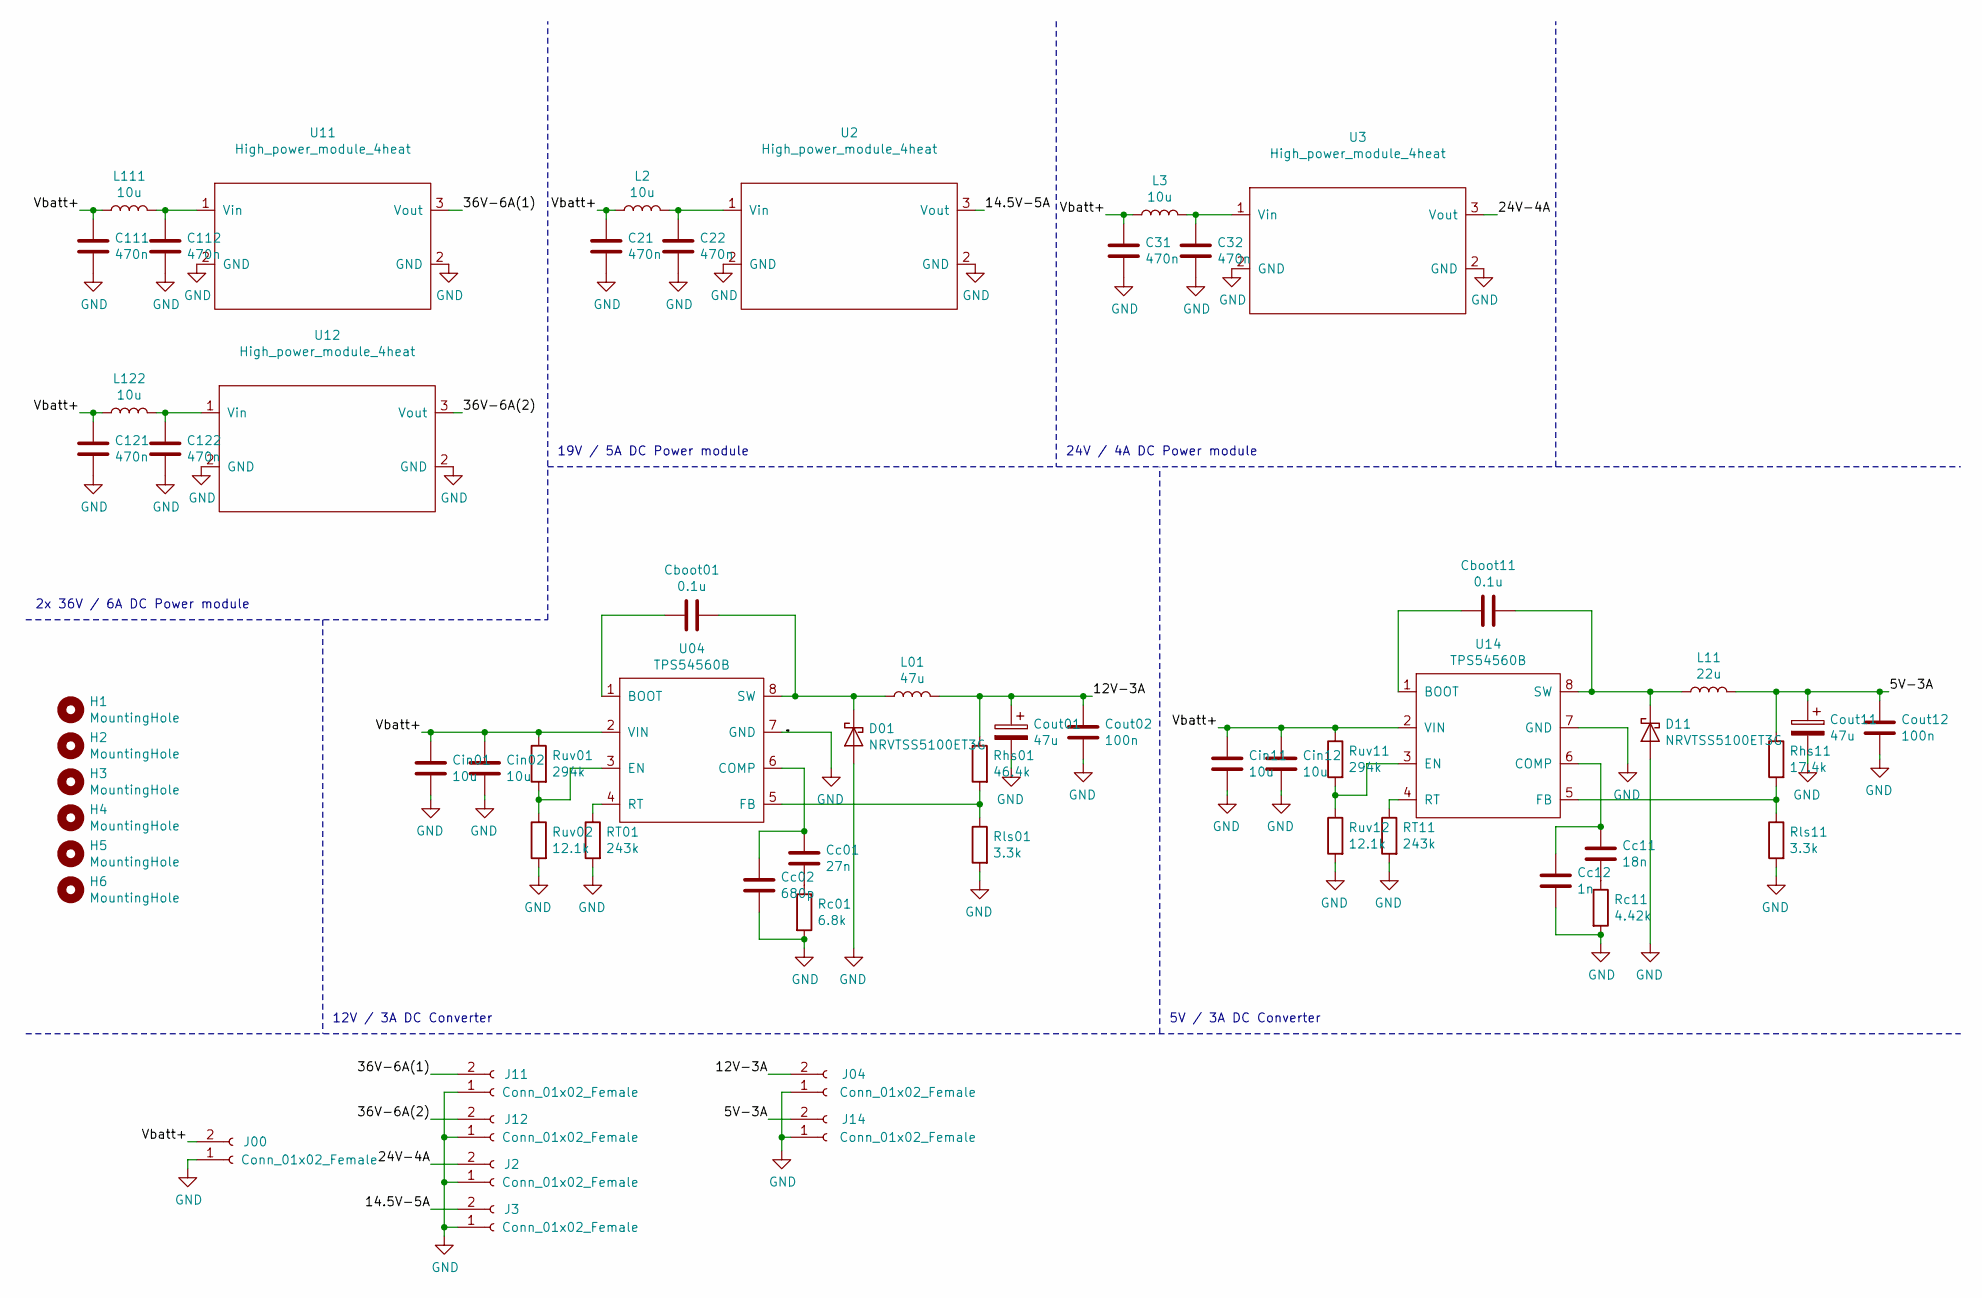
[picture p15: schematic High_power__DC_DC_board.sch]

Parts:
C21, C22, C31, C32, C111, C112, C121, C122: 470n; C_1210_3225Metric
Cboot01, Cboot11: 0.1u; C_0805_2012Metric
Cc01: 27n; C_0603_1608Metric
Cc02: 680p; C_0603_1608Metric
Cc11: 18n; C_0603_1608Metric
Cc12: 1n; C_0603_1608Metric
Cin01, Cin02, Cin11, Cin12: 10u; C_1210_3225Metric
Cout01, Cout11: 47u; CP_EIA-7343-40_Kemet-Y
Cout02, Cout12: 100n; C_0805_2012Metric
D01, D11: NRVTSS5100ET3G; D_SMB
H1, H2, H3, H4, H5, H6: MountingHole; MountingHole_3.2mm_M3
J00, J2, J3, J04, J11, J12, J14: Conn_01x02_Female; 172448-0004_Molex_2channel_horizontal
L01: 47u; 177CDMCC-DS
L2, L3: 10u; PA4341-XXXNLT
L11: 22u; 125CDMCCDS
L111, L122: 10u; 744373965100
RT01, RT11: 243k; R_0603_1608Metric
Rc01: 6.8k; R_0603_1608Metric
Rc11: 4.42k; R_0603_1608Metric
Rhs01: 46.4k; R_0603_1608Metric
Rhs11: 17.4k; R_0603_1608Metric
Rls01, Rls11: 3.3k; R_0603_1608Metric
Ruv01, Ruv11: 294k; R_0603_1608Metric
Ruv02, Ruv12: 12.1k; R_0603_1608Metric
U2, U3, U11, U12: High_power_module_4heat; DC_buck_boost_conv
U04, U14: TPS54560B; TPS54560BDDA

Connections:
/5V-3A: Cout11.1, Cout12.1, J14.2, L11.1, Rhs11.1
/12V-3A: Cout01.1, Cout02.1, J04.2, L01.1, Rhs01.1
/14.5V-5A: J3.2, U2.3 (Vout)
/24V-4A: J2.2, U3.3 (Vout)
/36V-6A(1): J11.2, U11.3 (Vout)
/36V-6A(2): J12.2, U12.3 (Vout)
/Vbatt+: C21.1, C31.1, C111.1, C121.1, Cin01.1, Cin02.1, Cin11.1, Cin12.1, J00.2, L2.2, L3.2, L111.2, L122.2, Ruv01.1, Ruv11.1, U04.2 (VIN), U14.2 (VIN)
GND: C21.2, C22.2, C31.2, C32.2, C111.2, C112.2, C121.2, C122.2, Cc02.1, Cc12.1, Cin01.2, Cin02.2, Cin11.2, Cin12.2, Cout01.2, Cout02.2, Cout11.2, Cout12.2, D01.2 (A), D11.2 (A), J00.1, J2.1, J3.1, J04.1, J11.1, J12.1, J14.1, RT01.2, RT11.2, Rc01.2, Rc11.2, Rls01.2, Rls11.2, Ruv02.2, Ruv12.2, U2.2 (GND), U3.2 (GND), U04.7 (GND), U04.9 (PAD), U11.2 (GND), U12.2 (GND), U14.7 (GND), U14.9 (PAD)
unnamed: C22.1, L2.1, U2.1 (Vin)
unnamed: C32.1, L3.1, U3.1 (Vin)
unnamed: C112.1, L111.1, U11.1 (Vin)
unnamed: C122.1, L122.1, U12.1 (Vin)
unnamed: Cboot01.1, D01.1 (K), L01.2, U04.8 (SW)
unnamed: Cboot01.2, U04.1 (BOOT)
unnamed: Cboot11.1, D11.1 (K), L11.2, U14.8 (SW)
unnamed: Cboot11.2, U14.1 (BOOT)
unnamed: Cc01.1, Rc01.1
unnamed: Cc01.2, Cc02.2, U04.6 (COMP)
unnamed: Cc11.1, Rc11.1
unnamed: Cc11.2, Cc12.2, U14.6 (COMP)
unnamed: RT01.1, U04.4 (RT)
unnamed: RT11.1, U14.4 (RT)
unnamed: Rhs01.2, Rls01.1, U04.5 (FB)
unnamed: Rhs11.2, Rls11.1, U14.5 (FB)
unnamed: Ruv01.2, Ruv02.1, U04.3 (EN)
unnamed: Ruv11.2, Ruv12.1, U14.3 (EN)

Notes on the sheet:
12V / 3A DC Converter
5V / 3A DC Converter
2x 36V / 6A DC Power module
19V / 5A DC Power module
24V / 4A DC Power module

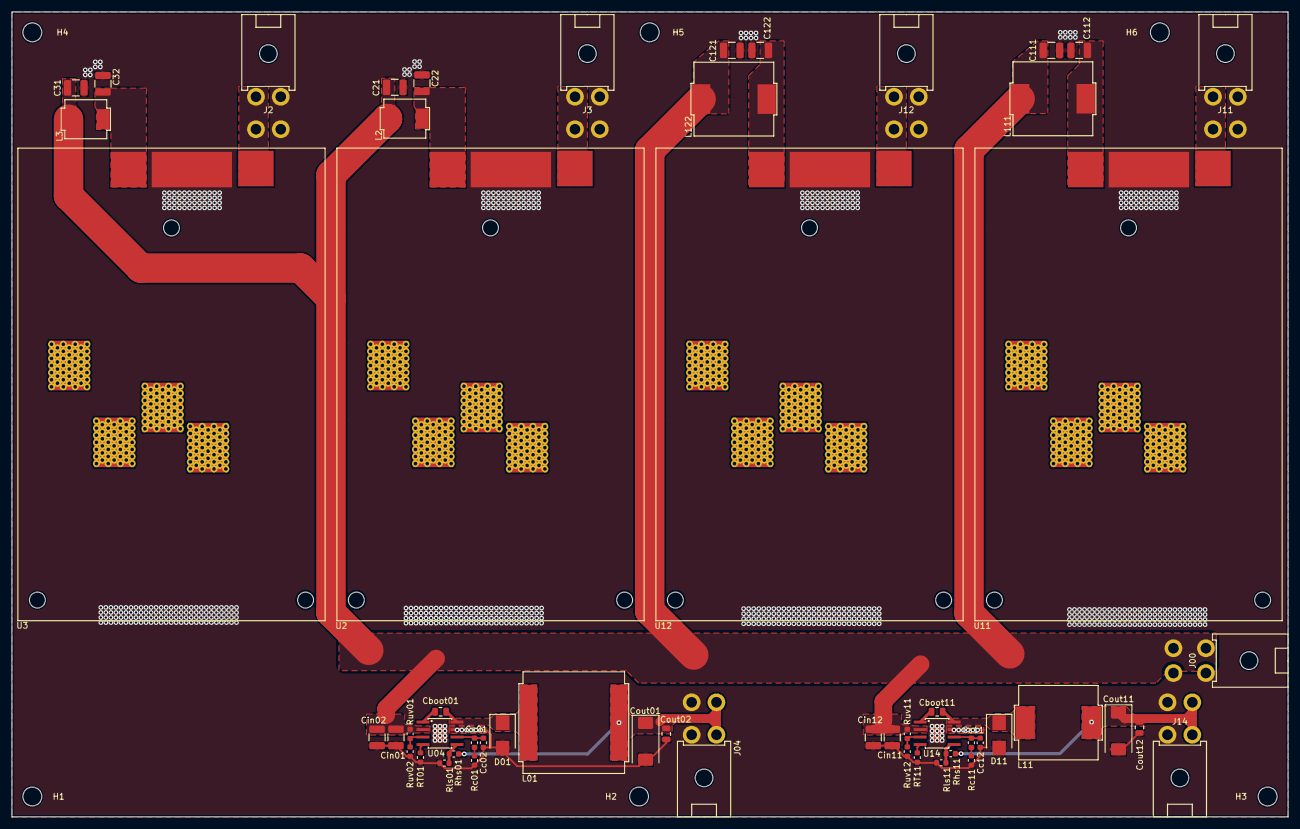
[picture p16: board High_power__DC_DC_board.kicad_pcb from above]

Board: 2 copper layers, 216.0 x 136.2 mm, 61 parts (0 on the bottom side), 26 nets.

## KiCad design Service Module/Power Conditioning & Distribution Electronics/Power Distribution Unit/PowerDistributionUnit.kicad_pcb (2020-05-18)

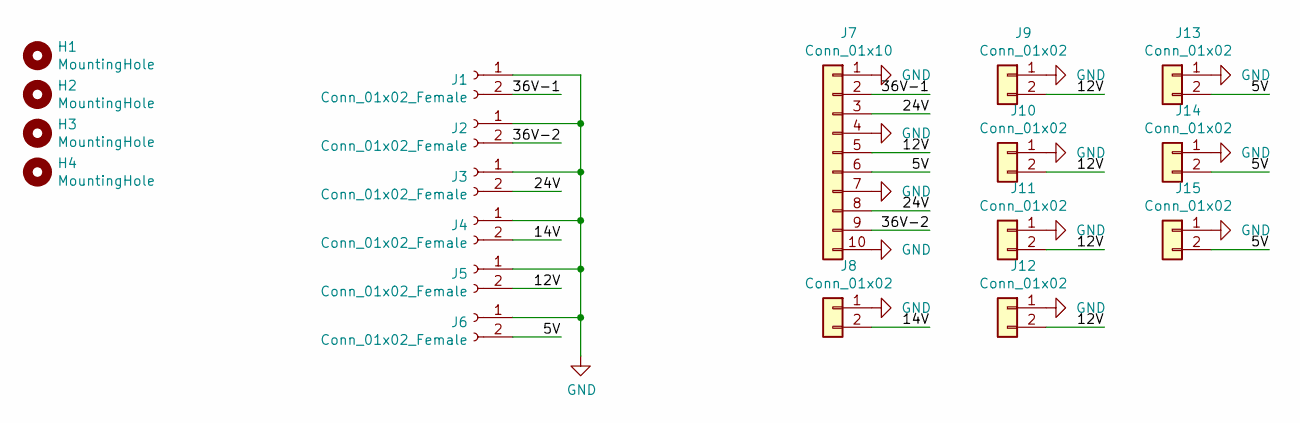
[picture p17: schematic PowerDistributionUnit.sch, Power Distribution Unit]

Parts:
H1, H2, H3, H4: MountingHole; MountingHole_3.2mm_M3
J1, J2, J3, J4, J5, J6: Conn_01x02_Female; 172448-0004_Molex_2channel_horizontal
J7: Conn_01x10; JST_VH_B10P-VH
J8: Conn_01x02; JST_VH_B2P-VH
J9, J10, J11, J12, J13, J14, J15: Conn_01x02; JST_XA_B2B-XASK-1

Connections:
/5V: J6.2, J7.6, J13.2, J14.2, J15.2
/12V: J5.2, J7.5, J9.2, J10.2, J11.2, J12.2
/14V: J4.2, J8.2
/24V: J3.2, J7.3, J7.8
/36V-1: J1.2, J7.2
/36V-2: J2.2, J7.9
GND: J1.1, J2.1, J3.1, J4.1, J5.1, J6.1, J7.1, J7.4, J7.7, J7.10, J8.1, J9.1, J10.1, J11.1, J12.1, J13.1, J14.1, J15.1

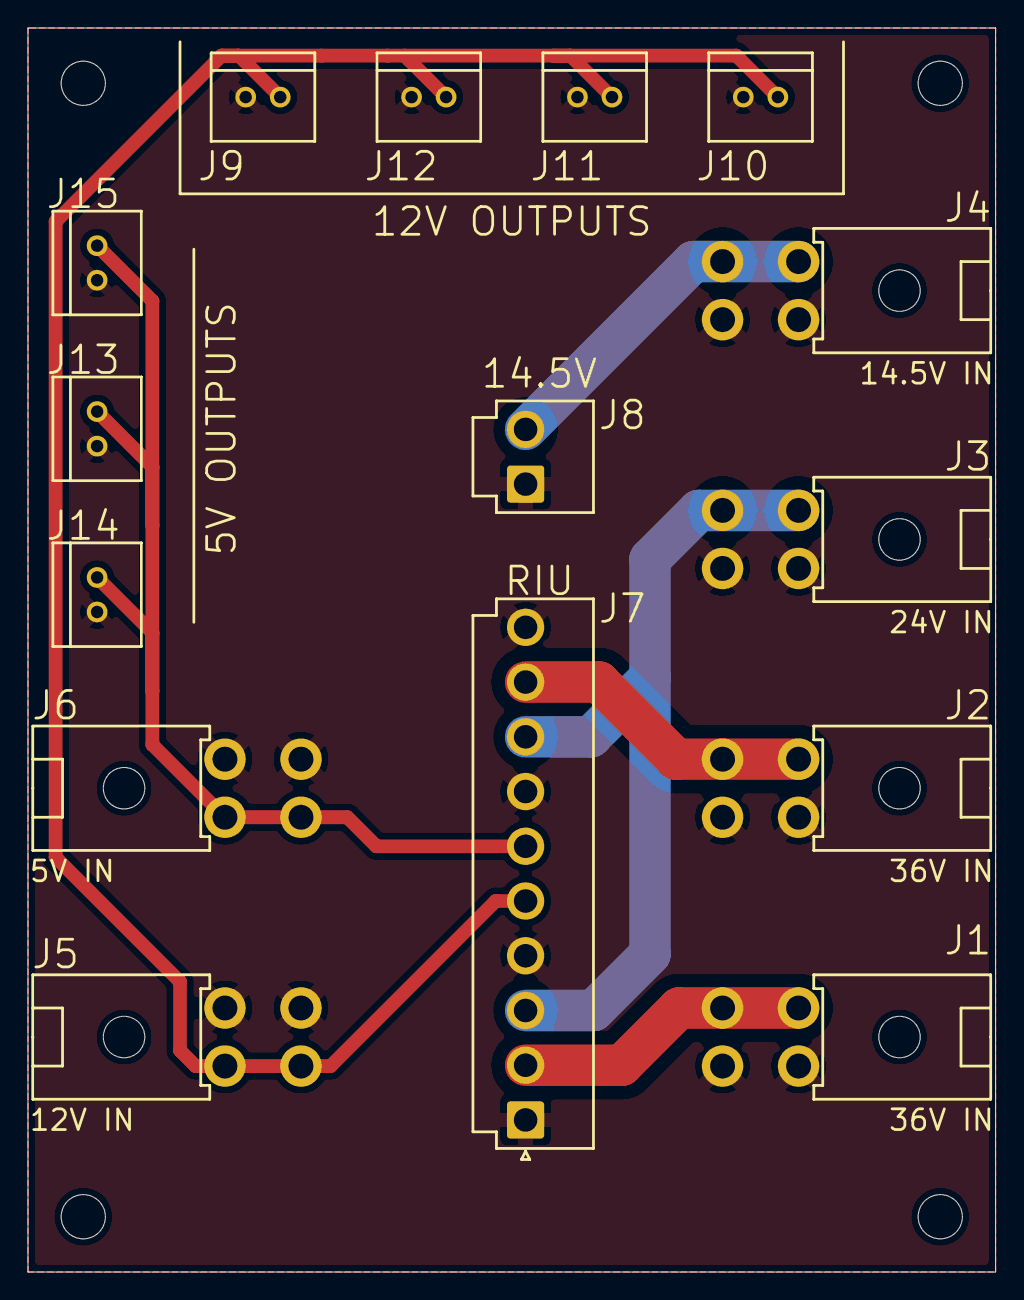
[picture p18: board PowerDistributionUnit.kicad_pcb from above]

Board: 2 copper layers, 70.0 x 90.0 mm, 19 parts (0 on the bottom side), 7 nets.
